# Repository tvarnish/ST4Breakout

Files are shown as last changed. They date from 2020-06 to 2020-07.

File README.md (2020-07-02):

# ST-4 Autoguider Breakout board 
An open-source, versatile breakout board for controlling ST-4 autoguider ports on telescope mounts. Connect the board to the drive motors with an ST-4 cable (RJ12) and use a 5V microcontroller (e.g. Raspberry Pi GPIO or Arduino) to easily control the motor axes!

> :warning: **IMPORTANT:** I've only tested this with a **Skywatcher Enhanced Dual-Axis Motor Drive for EQ3-2 Mount**, so I can't guarantee it'll work with every autoguider-compatible telescope mount! If you've tried this on another 'scope, let me know if it was successful!

<p align="center">
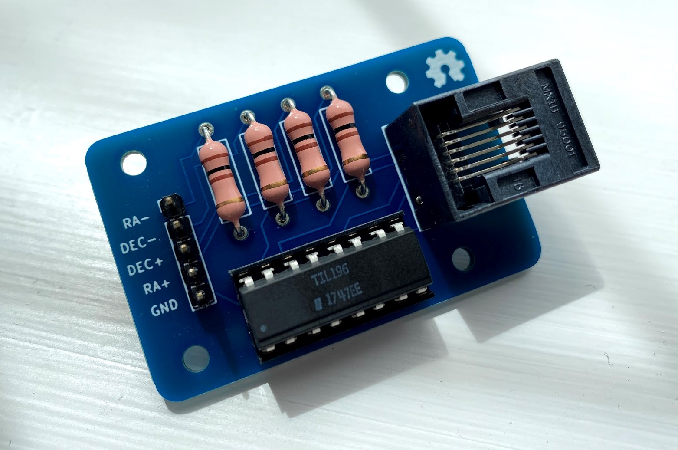
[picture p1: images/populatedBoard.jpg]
Completed project PCB with soldered components.
    
</p>

To trigger an axis, pull the corresponding input header pin HIGH (5V). This breakout board can be used for dual-axis control at a single slewing speed (set by the motor drive handset).

> :warning: **ANOTHER IMPORTANT NOTE:** Only trigger a single axis (HIGH) at a time. There isn't anything (yet) in the hardware that will prevent this, so make sure it doesn't ever happen through software.

I had the v0.1 board printed with [JLCPCB](https://jlcpcb.com/), as seen in the image above.

All of the KiCAD files (and gerbers) for the breakout can be found in the `/ST4Breakout` directory.

## Required Components
To construct the board, along with the PCB you'll also need the following components:

Component | Quantity
----------|---------
[RJ12 Socket](https://uk.rs-online.com/web/p/products/2400929/) | 1
[100 Ohm Resistor](https://uk.rs-online.com/web/p/products/7078625/) | 4
[TIL196 Phototransistor Optocoupler](https://uk.rs-online.com/web/p/products/1611233/) | 1
[16-pin IC DIP Socket](https://uk.rs-online.com/web/p/products/0402771/) | 1
[Single-row 2.54 mm Header Pins](https://uk.rs-online.com/web/p/products/2518632/) | 5 pins

*(All links provided are for RS Components UK)*
Component footprints and 3D models are provided for these specified components. Equivalent parts may work, but their footprints may be slightly different, so I can't guarantee they'll fit the PCB.

## Additional Board Images

<p align="center">
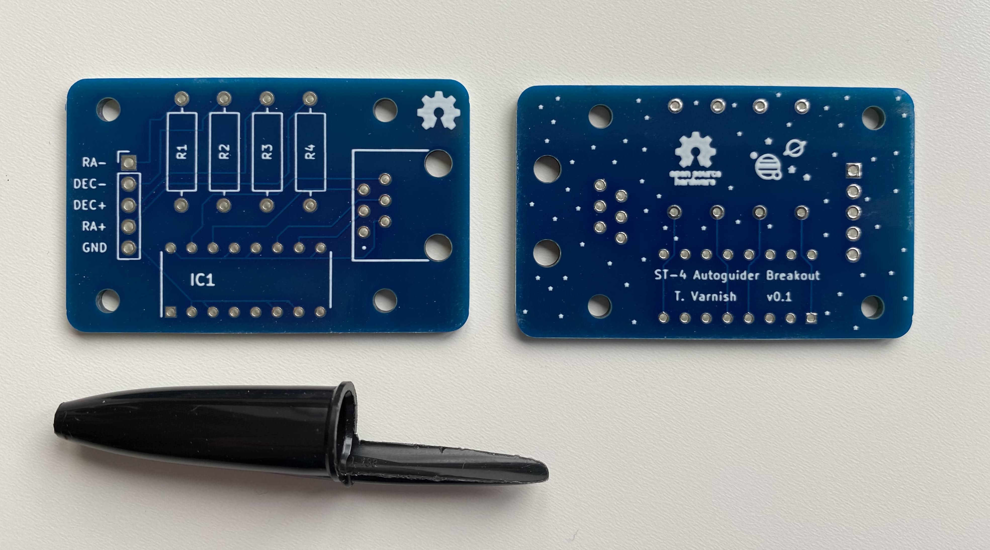
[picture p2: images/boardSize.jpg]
Front and back of the board (unpopulated).
    
</p>

Front and back of the board (unpopulated). Ballpoint pen lid for scale. I thought a banana would be a bit too big. And... I didn't have one to hand.

<p align="center">
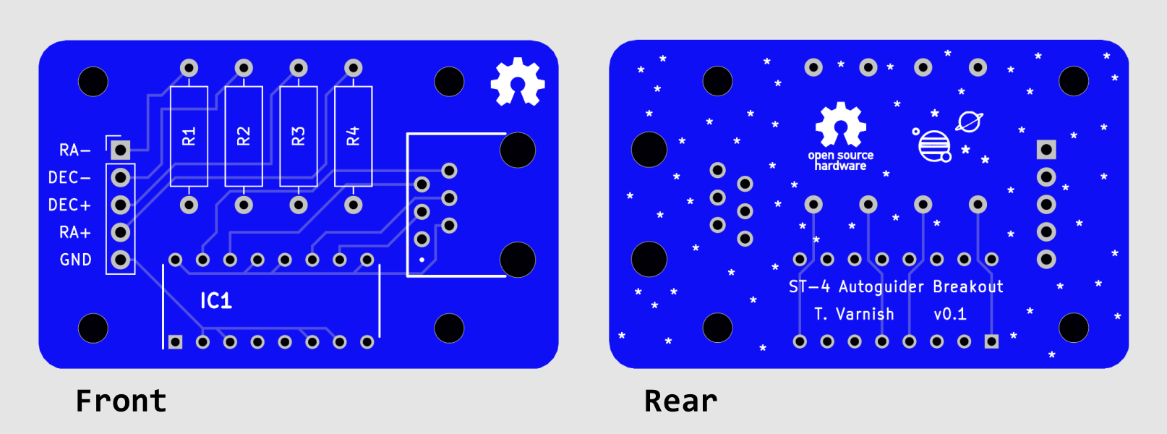
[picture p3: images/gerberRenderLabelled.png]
Gerber renders for the front and back of the PCB.
    
</p>

Gerber renders for the front and back of the PCB.

## Circuit Description
I've provided a basic explanation for the operation of the breakout board below, in case it helps you to decide if the board will work for your mount (if it isn't a Skywatcher EQ3-2). **Note: I can't guarantee if this will work for your mount/drive! Use at your own risk!**

Each "axis" (e.g. RA/DEC) has a positive and negative trigger pin (to drive the motor forwards or backwards). Applying a 5V signal to one of these pins will "trigger" the telescope axis to move in that specific direction.

Each trigger pin is connected (via a current limiting resistor) to one input of a quad-input optocoupler IC (TIL196). This connects the microcontroller circuit to the telescope motor drive circuit, isolating each side. Triggering an axis will connect the corresponding wire in the ST-4 cable to ground, completing the controller-side circuit. The optocoupler IC is necessary to ensure that the higher voltage/current on the motor controller side doesn't break the microcontroller!

<p align="center">
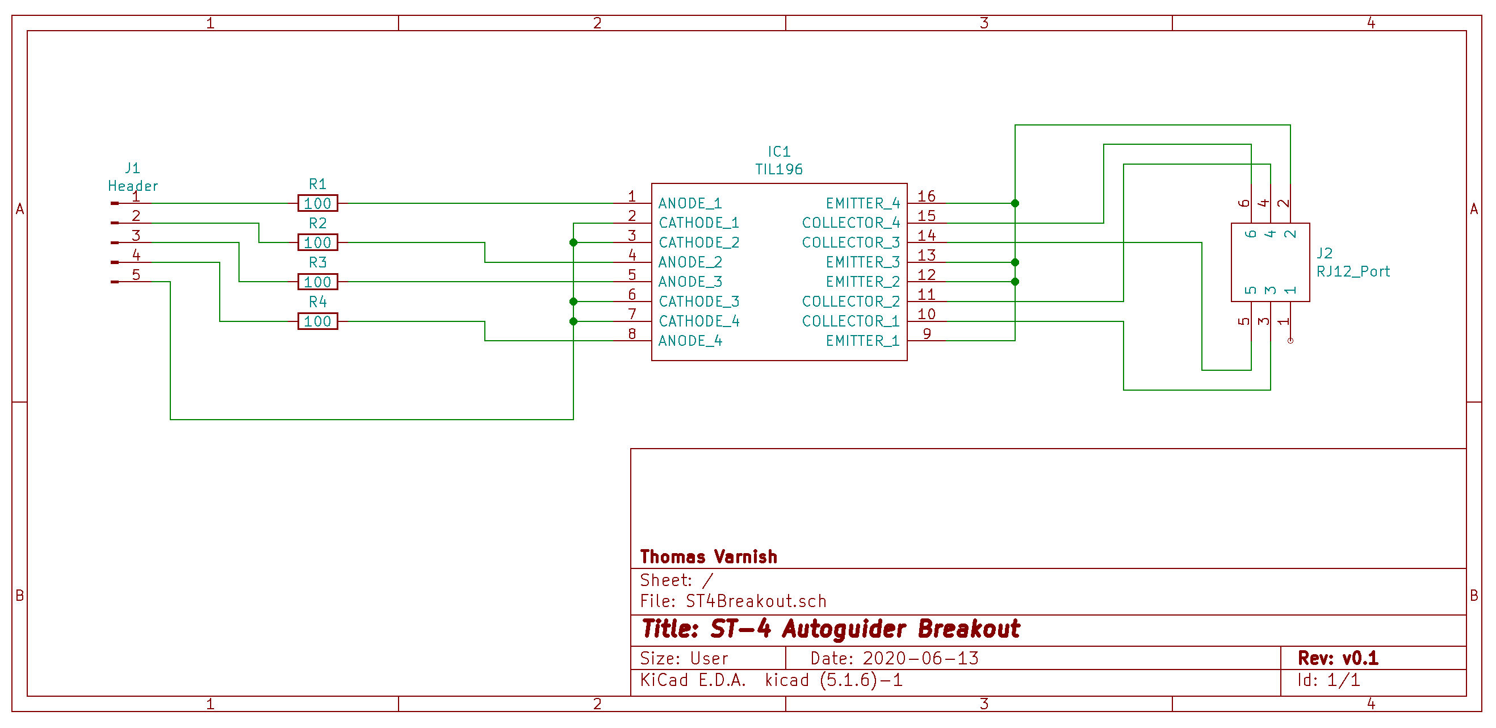
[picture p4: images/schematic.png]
Labelled schematic for the breakout board.
    
</p>

## Author
Created by Thomas Varnish. Find me [@tvarnish](https://github.com/tvarnish) on GitHub and [@ThomasVarnish](https://twitter.com/ThomasVarnish) on Twitter :smiley:

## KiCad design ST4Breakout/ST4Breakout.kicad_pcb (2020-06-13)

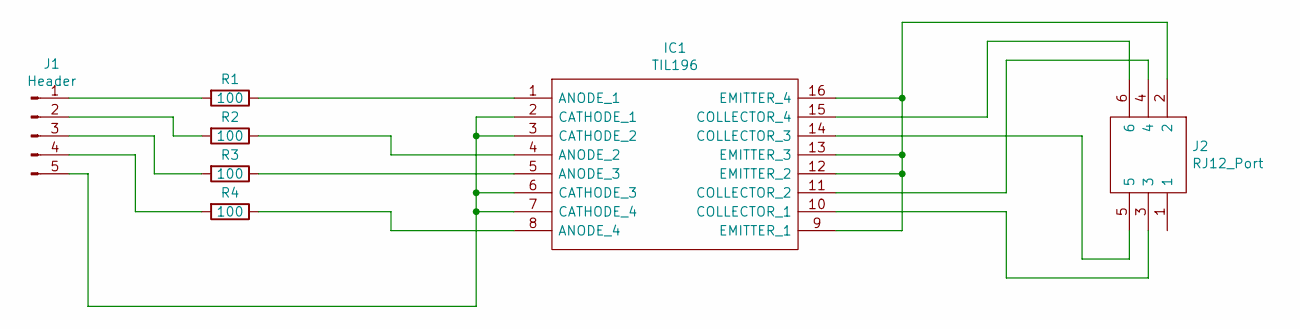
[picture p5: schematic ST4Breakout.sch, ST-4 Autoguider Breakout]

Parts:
IC1: TIL196; TIL196_Optocoupler_THT; Manufacturer_Part_Number TIL196
J1: Header; PinHeader_1x05_P2.54mm_Vertical
J2: RJ12_Port; RJ12_Female_THT_Connector; Manufacturer_Part_Number 95501-2661; Mouser Part Number 538-95501-2661
R1, R2, R3, R4: 100; R_Axial_DIN0309_L9.0mm_D3.2mm_P12.70mm_Horizontal

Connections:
unnamed: IC1.1 (ANODE_1), R1.1
unnamed: IC1.2 (CATHODE_1), IC1.3 (CATHODE_2), IC1.6 (CATHODE_3), IC1.7 (CATHODE_4), J1.5
unnamed: IC1.4 (ANODE_2), R2.1
unnamed: IC1.5 (ANODE_3), R3.1
unnamed: IC1.8 (ANODE_4), R4.1
unnamed: IC1.10 (COLLECTOR_1), J2.3
unnamed: IC1.11 (COLLECTOR_2), J2.4
unnamed: IC1.9 (EMITTER_1), IC1.12 (EMITTER_2), IC1.13 (EMITTER_3), IC1.16 (EMITTER_4), J2.2
unnamed: IC1.14 (COLLECTOR_3), J2.5
unnamed: IC1.15 (COLLECTOR_4), J2.6
unnamed: J1.1, R1.2
unnamed: J1.2, R2.2
unnamed: J1.3, R3.2
unnamed: J1.4, R4.2

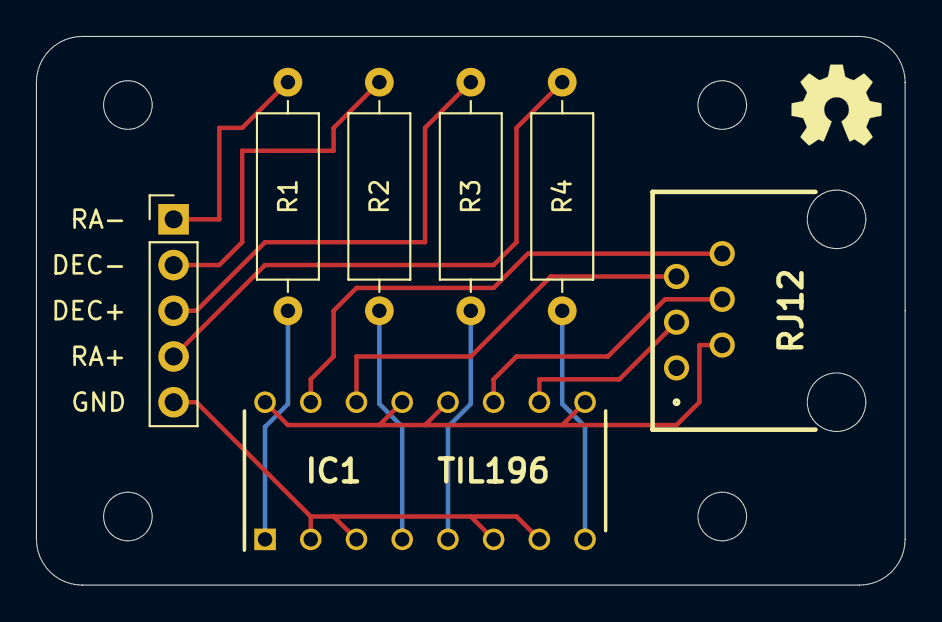
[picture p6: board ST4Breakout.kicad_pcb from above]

Board: 2 copper layers, 48.3 x 30.5 mm, 7 parts (0 on the bottom side), 14 nets.

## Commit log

2020-07-02 Add schematic to README.md
2020-07-02 Update README.md
    Fix the wording of the circuit description.
